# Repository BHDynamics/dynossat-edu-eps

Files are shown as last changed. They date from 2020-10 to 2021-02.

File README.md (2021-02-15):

# DynOSSAT-EDU-EPS (Electric Power System)
DynOSSAT-EDU is the first open source PocketQube educational kit compatible with CircuitPython and Arduino.

This plaform is equipped with all the necessary modules for the operation of a nanosatellite (PocketQube)
in Low Earth Orbit (LEO) that would serve as a device for teaching, training, and driving curiosity about the philosophy and technology related to NewSpace.

This repository contains the hardware files for the EPS (Electric Power System), the module responsible for battery management and power distribution subsystems,
including charging through solar panels using flight-proven MPPT electronics.

Hardware in this repository is licenced under **CERN OHL v1.2**.

## Technical details

- Well-known 48 MHz Cortex-M0 ATSAMD21E18 MCU with 256 KB flash + 32 KB RAM
- 32 Mbit SPI flash for storing CircuitPython code and libraries
- Flight-proven SPV1040 Maximum Power Point Tracking (MPPT) IC for solar cells power management
- Ultra low input voltage L6924D Lithium battery charger management IC optimized for pairing with the SPV1040
- Separate 5V and 3.3V power rails generated through high-performance DC/DC converters
- Battery Current/Voltage/Power measurement through the flight-proven INA226 digital meter
- Back-powering protection and load switching through the TPS22918, member of a flight-proven family of switches
- User-controllable WS2812B addressable RGB LED
- Female USB-C 2.0 connector for power and data logging
- Standard Molex Picoblade 1.5 mm connectors for battery and solar cells
- Connected to the OBC through SPI/I2C/UART for data communication and/or redundancy

## Documentation

Available in this repo's [Wiki](https://github.com/BHDynamics/dynossat-edu-eps/wiki).

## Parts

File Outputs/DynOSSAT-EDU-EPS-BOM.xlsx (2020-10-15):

Item | Qty | Reference(s) | Value | Part Number | Comments
1 | 2 | C1, C2 | 22pF |  | 0402 NP0 22pF
2 | 2 | C3, C17 | 1nF |  | 0402 NP0 1nF
3 | 10 | C4, C5, C6, C7, C8, C9, C14, C19, C23, C29 | 100nF |  | 0402 X7R/X5R 100nF
4 | 3 | C10, C12, C26 | 10nF |  | 0402 X7r/X5R 100nF
5 | 4 | C11, C18, C25, C27 | 1uF |  | 0402 1uF 10V or greater X5R or better
6 | 2 | C13, C30 | 10uF |  | 0603 10uF 10V or greater X5R or better
7 | 5 | C15, C16, C20, C22, C24 | 22uF |  | 0603 22uF 10V or greater X5R or better
8 | 1 | C21 | 4.7uF |  | 0603 4.7uF 10V or greater X5R or better
9 | 1 | C28 | 1uF |  | 0603 1uF 10V or greater X5R or better
10 | 2 | C31, C32 | 220uF | GRM31CR60J227ME11L | 1206 6.3V 220 uF
11 | 1 | D1 | WS2812B-MINI | WS2812B-MINI | RGB LED
12 | 2 | D2, D3 | LED_Small |  | 0603 LED. D2 Red, D3 Green
13 | 1 | D4 | LED_Small | SD05-01FTG | 5V TVS Diode SOD-323
14 | 5 | D5, D7, D8, D9, D10 | D_Schottky_Small | CUS10S30,H3F | Diode_SMD:D_SOD-323
15 | 1 | D6 | D_Schottky_Small | 1N5819HWQ-7-F | Diode_SMD:D_SOD-123
16 | 1 | F1 | Fuse_3A | T0603FF3000TM | Fuse:Fuse_0603_1608Metric
17 | 1 | J1 | Conn_01x05_Female | - | Connector_PinHeader_1.27mm:PinHeader_1x05_P1.27mm_Vertical
18 | 1 | J2 | USB_C_Receptacle_USB2.0 | U262-161N-4BVC11 | DynOSSAT:U262-161N-4BVC11
19 | 1 | J4 | PV Panel 1 | 53048-0210 | Connector_Molex:Molex_PicoBlade_53048-0210_1x02_P1.25mm_Horizontal
20 | 1 | J5 | PV Panel 2 | 53048-0210 | Connector_Molex:Molex_PicoBlade_53048-0210_1x02_P1.25mm_Horizontal
21 | 1 | J6 | Battery | 53048-0210 | Connector_Molex:Molex_PicoBlade_53048-0210_1x02_P1.25mm_Horizontal
22 | 1 | J7 | Main Bus PQBH40 | We don't have part numbers. Use generic brand | Pin header male 1.27mm pitch 2x20 vertical SMD
23 | 1 | J8 | Main Bus PQBH40 | We don't have part numbers. Use generic brand | Pin socket female 1.27mm pitch 2x20 vertical SMD
24 | 1 | JP1 | Jumper | We don't have part numbers. Use generic brand | Pin header male 1.27mm pitch 1x02 Vertical Through-Hole
25 | 1 | JP2 | Jumper | - | Solder jumper
26 | 1 | L1 | 22uH | SMNR4030-220MT | Inductor_SMD:L_Bourns-SRN4018
27 | 1 | L2 | 2.2uH | LQH32PN2R2NN0L | 1210 2.2uH Power Inductor
28 | 1 | L3 | 3.3uH | LQH32PN3R3NN0L | 1210 3.3uH Power Inductor
29 | 1 | Q1 | SQ3989EV | SQ3989EV-T1_GE3 | Dual P-Channel Mosfet
30 | 1 | Q2 | DMG2305 | DMG2305UX-7 | P-Channel Power Mosfet
31 | 7 | R1, R2, R3, R11, R18, R27, R32 | 100k |  | 0402 100k 1%
32 | 1 | R4 | 510R |  | 0402 510R 1%
33 | 2 | R5, R6 | 10k |  | 0402 10k 1%
34 | 1 | R7 | 0.002R | LVT06R0020HER | 0603 0.002R Current Shunt
35 | 2 | R10, R25 | 1M |  | 0402 1M
36 | 2 | R12, R13 | 330R |  | 0402 330R
37 | 3 | R14, R15, R16 | 1k |  | 0402 1k
38 | 1 | R17 | 0.033R | WSL0603R0330FEA | 0603 0.033R Current Shunt
39 | 1 | R19 | 22k2 |  | 0402 22.2k
40 | 1 | R20 | 2.2M |  | 0402 2.2M
41 | 1 | R21 | 820k |  | 0402 820k
42 | 2 | R22, R23 | 5.1k |  | 0402 5.1k
43 | 1 | R24 | 10M |  | 0402 10M
44 | 1 | R26 | 1.5M |  | 0402 1.5M
45 | 4 | R8, R9, R29, R33 | 47k |  | 0402 47k
46 | 1 | R30 | 88k |  | 0402 88k
47 | 2 | R31, R35 | 12k |  | 0402 12k
48 | 1 | R36 | 3k3 |  | 0402 3k3
49 | 1 | SW1 | SW_Push | 1TS002G-1800-3500-CT | Push Button side mount
50 | 1 | SW2 | SW_SPDT | OS102011MA1QN1 | SPDT switch
51 | 1 | U1 | ATSAMD21G18A | ATSAMD21G18A-MUT | MCU
52 | 1 | U2 | GD25Q32 | GD25Q32CNIGR | 32 Mbit flash memory SPI
53 | 1 | U3 | INA226 | INA226AIDGSR | Current/Voltage monitoring IC
54 | 1 | U4 | FP6291 | FP6291LR-G1 | Step-Up 2A DC-DC Boost Converter
55 | 4 | U5, U9, U10, U11 | TPS22918 | TPS22918DBVR | Load Switch
56 | 1 | U6 | SPV1040 | SPV1040T | Solar Power Harvester
57 | 1 | U7 | SY8089 | SY8089AAC | Step-Down 2A DC-DC Buck Converter
58 | 1 | U8 | L6924D | L6924D | Low Vin Battery Charger IC
59 | 1 | Y1 | 32.768 kHz - 12.5pF | X201232768KGD2SI | 2012 32768 kHz Crystal 12.5pF
For passives (resistors, capacitors, etc) you may use any quality brand while meeting requirements

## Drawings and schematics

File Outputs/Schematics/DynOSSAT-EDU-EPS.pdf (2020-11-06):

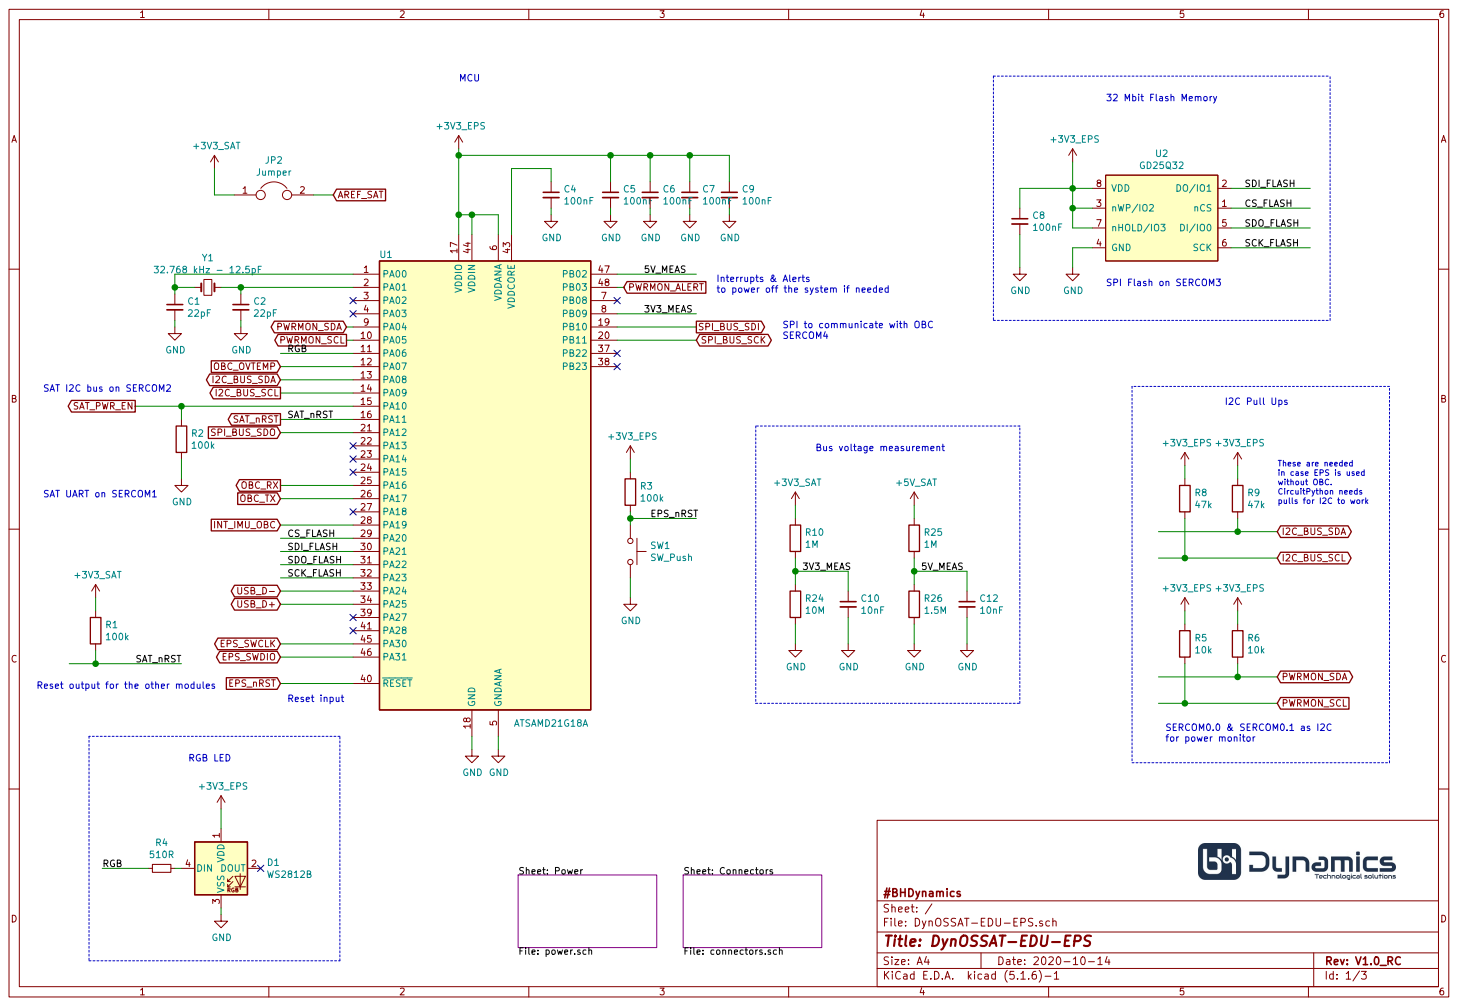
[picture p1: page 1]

in case EPS is used without OBC. CircuitPython needs pulls for I2C to work MCU

32 Mbit Flash Memory RGB LED

Interrupts & Alerts
to power off the system if needed

Id: 1/3 Title: DynOSSAT-EDU-EPS

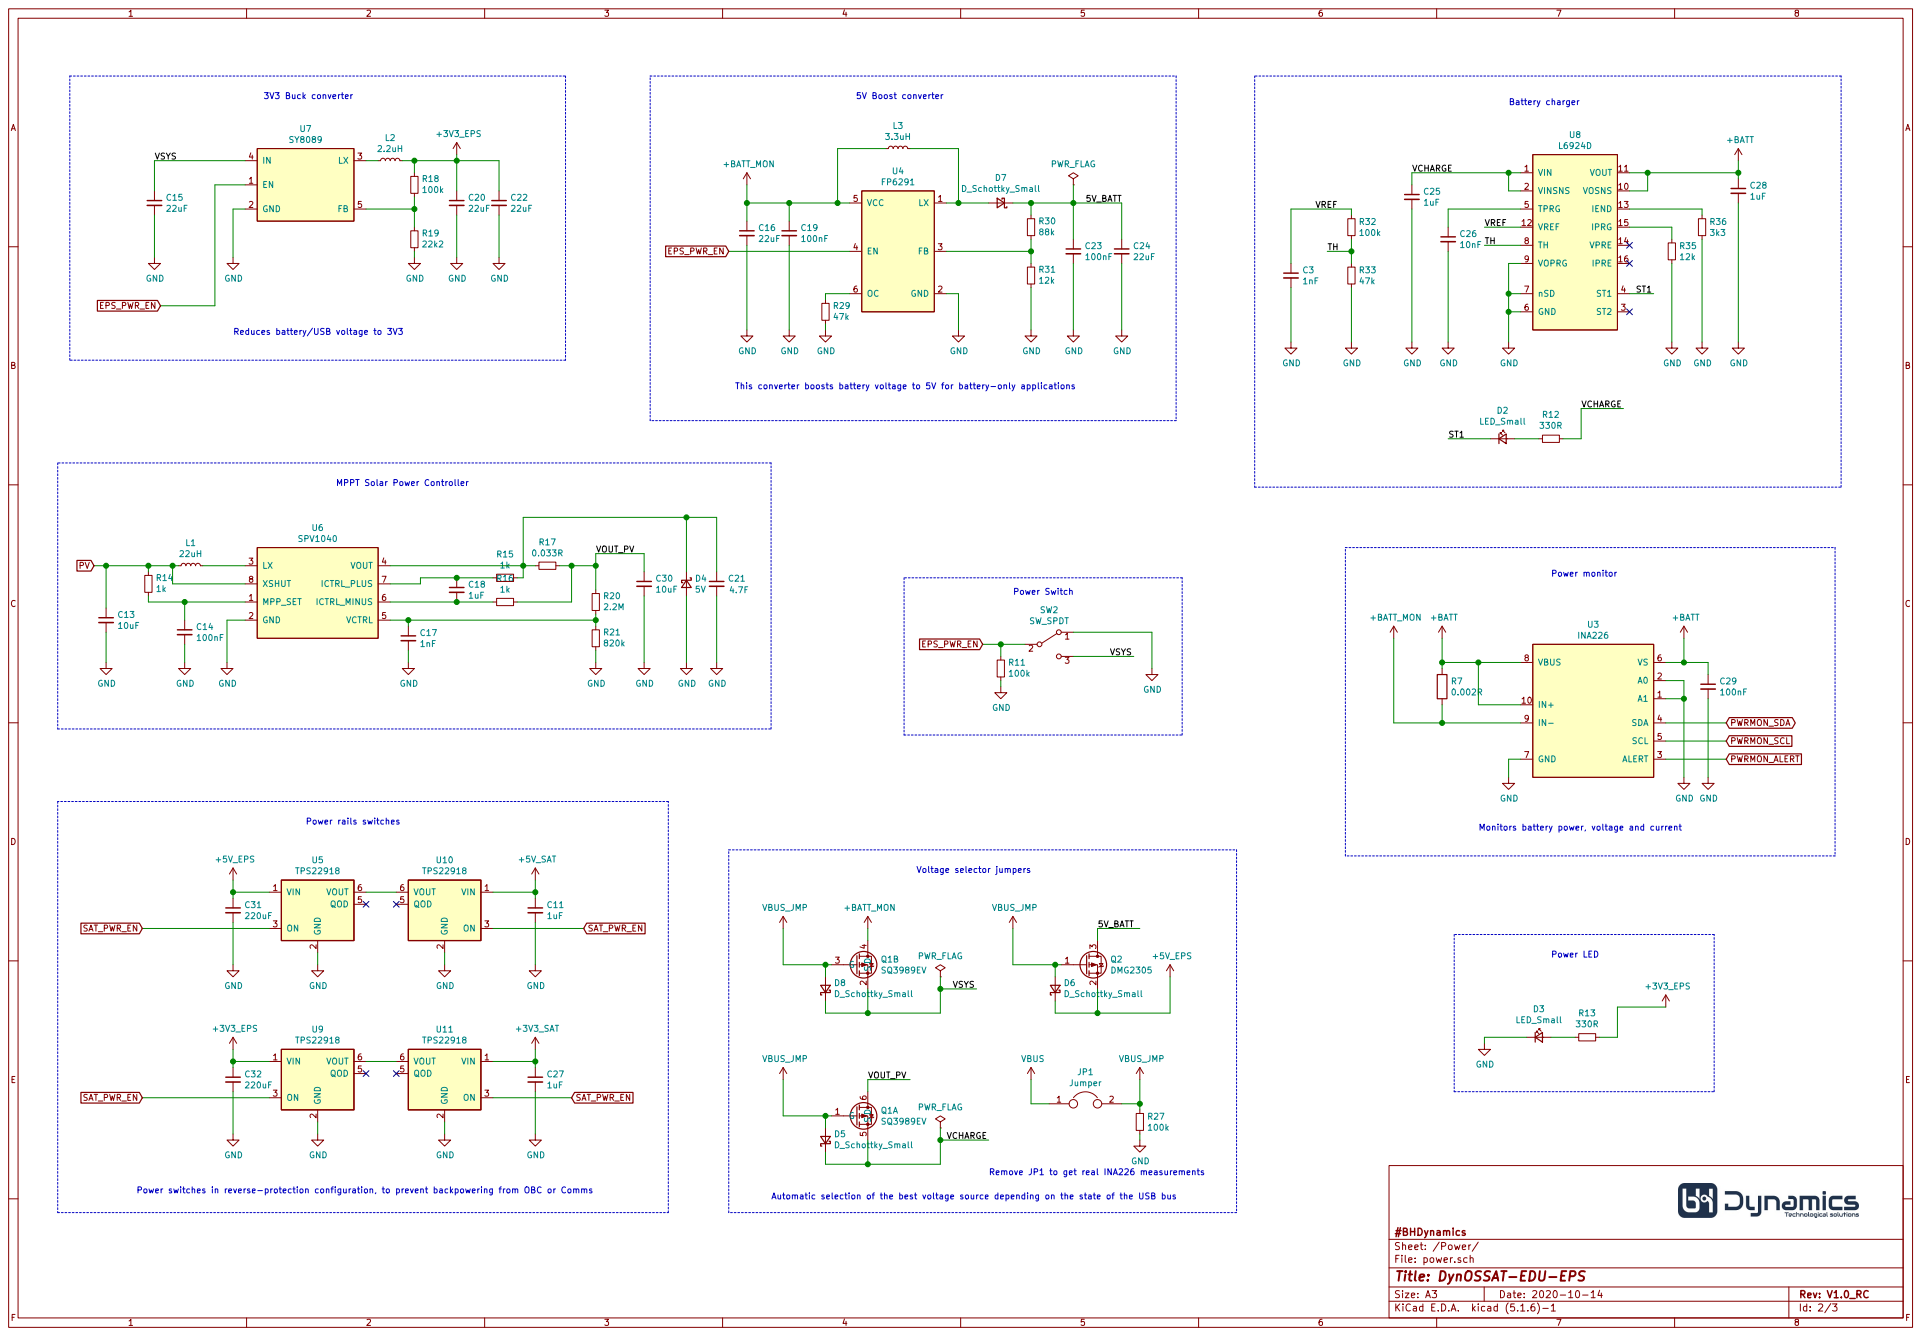
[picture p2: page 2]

2 ON 3 QOD 5 VOUT 6 U5 TPS22918 VIN 1 GND

2 ON 3 QOD 5 VOUT 6 U10 TPS22918 GND

2 ON 3 QOD 5 VOUT 6 U11 TPS22918 GND

Remove JP1 to get real INA226 measurements

Power switches in reverse-protection configuration, to prevent backpowering from OBC or Comms

File: power.sch Sheet: /Power/ #BHDynamics

Id: 2/3 Title: DynOSSAT-EDU-EPS

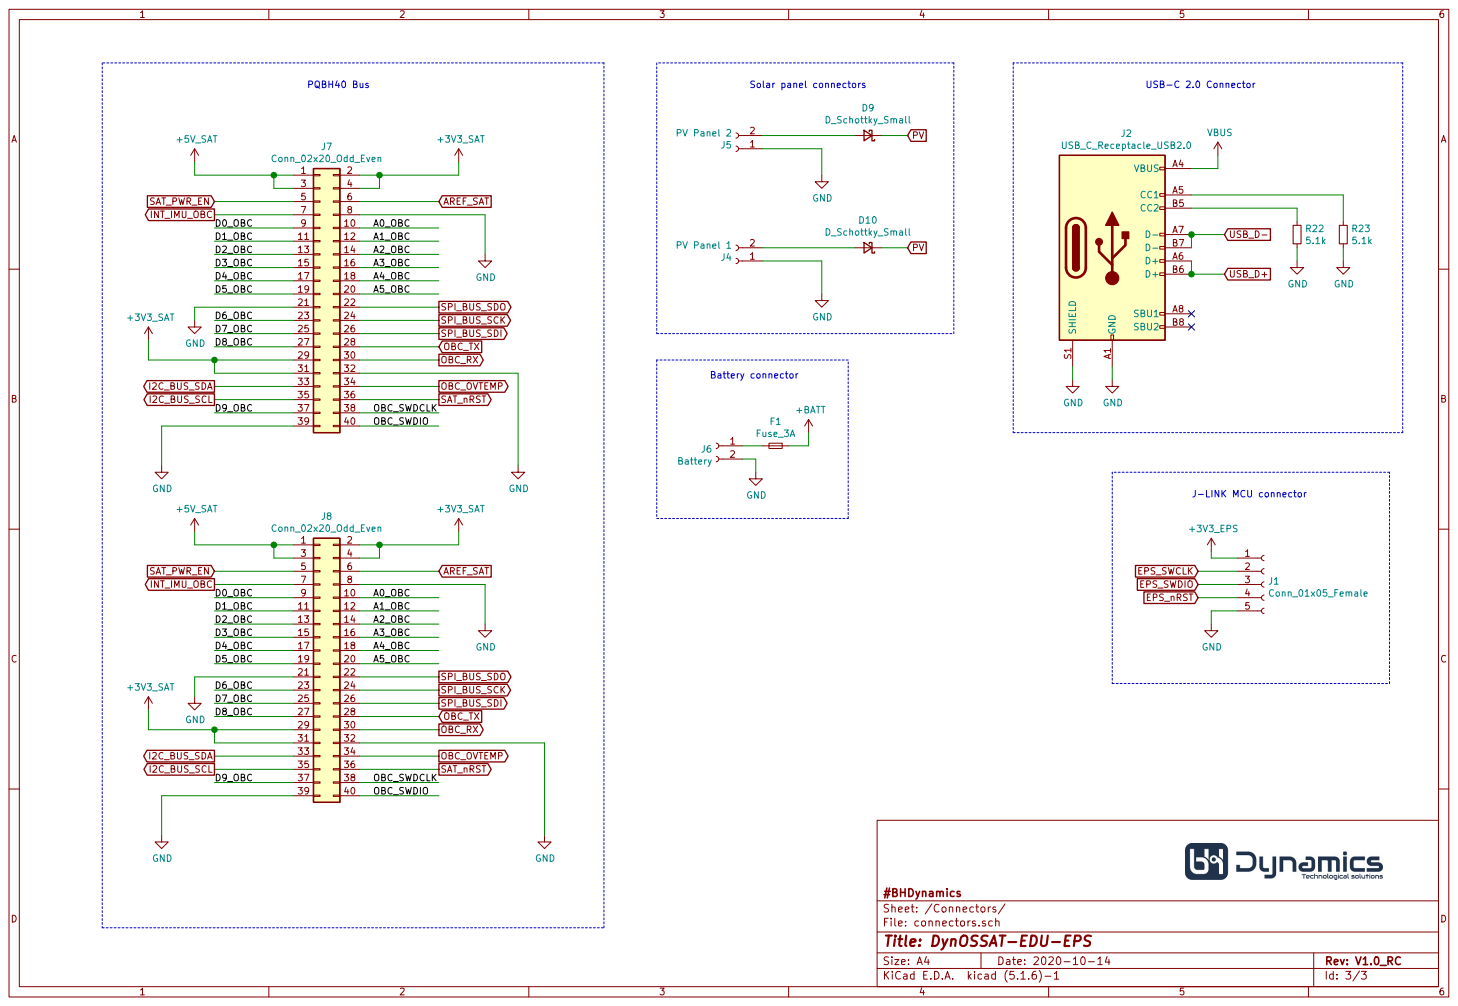
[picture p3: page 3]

File: connectors.sch Sheet: /Connectors/ #BHDynamics

Id: 3/3 Title: DynOSSAT-EDU-EPS

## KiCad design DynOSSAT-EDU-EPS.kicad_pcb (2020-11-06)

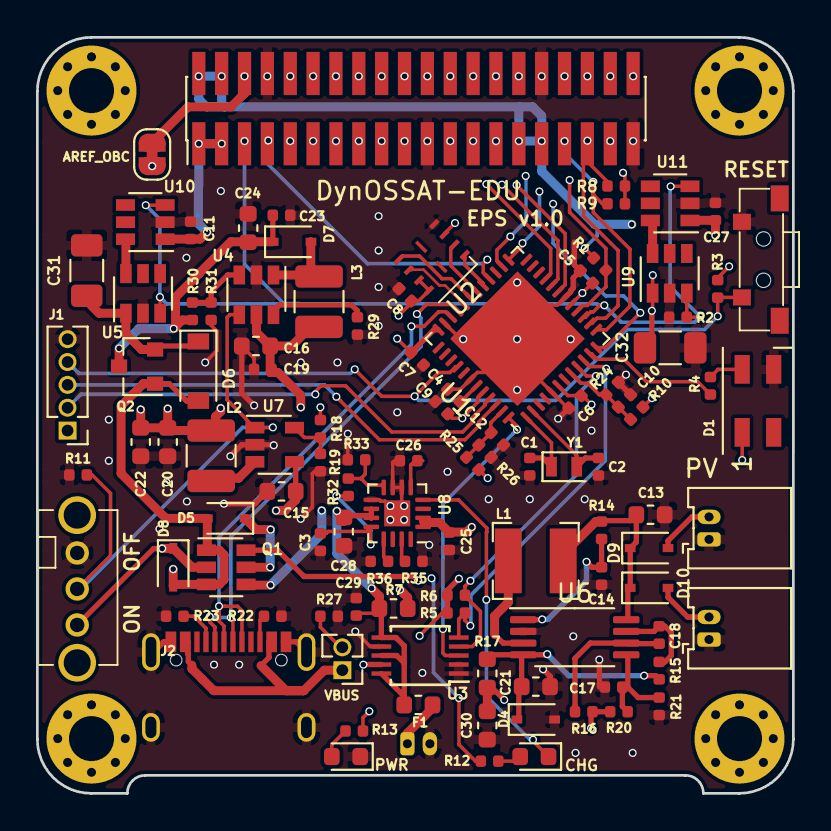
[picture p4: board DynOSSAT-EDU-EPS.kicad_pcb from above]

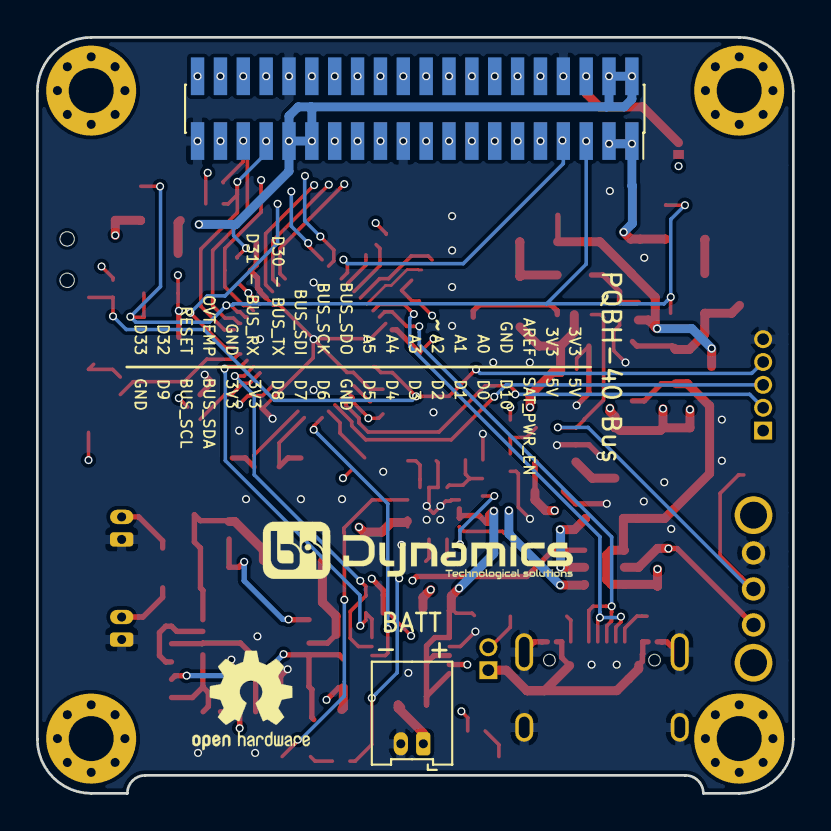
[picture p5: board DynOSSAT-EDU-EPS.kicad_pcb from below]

Board: 4 copper layers, 42.0 x 42.0 mm, 105 parts (2 on the bottom side), 90 nets.

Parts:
C1, C2: 22pF; C_0402_1005Metric
C3, C17: 1nF; C_0402_1005Metric
C4, C5, C6, C7, C8, C9, C14, C19, C23, C29: 100nF; C_0402_1005Metric
C10, C12, C26: 10nF; C_0402_1005Metric
C11, C18, C25, C27: 1uF; C_0402_1005Metric
C13, C30: 10uF; C_0603_1608Metric
C15, C16, C20, C22, C24: 22uF; C_0603_1608Metric
C21: 4.7F; C_0603_1608Metric
C28: 1uF; C_0603_1608Metric
C31, C32: 220uF; C_1206_3216Metric
D1: WS2812B; LED_SK6812MINI_PLCC4_3.5x3.5mm_P1.75mm
D2, D3: LED_Small; LED_0603_1608Metric
D4: 5V; D_SOD-323
D5, D7, D8, D9, D10: D_Schottky_Small; D_SOD-323
D6: D_Schottky_Small; D_SOD-123
F1: Fuse_3A; Fuse_0603_1608Metric
J1: Conn_01x05_Female; PinHeader_1x05_P1.27mm_Vertical
J2: USB_C_Receptacle_USB2.0; U262-161N-4BVC11
J4: PV Panel 1; Molex_PicoBlade_53048-0210_1x02_P1.25mm_Horizontal
J5: PV Panel 2; Molex_PicoBlade_53048-0210_1x02_P1.25mm_Horizontal
J6: Battery; Molex_PicoBlade_53048-0210_1x02_P1.25mm_Horizontal
J7: Conn_02x20_Odd_Even; PinHeader_2x20_P1.27mm_Vertical_SMD
J8: Conn_02x20_Odd_Even; PinSocket_2x20_P1.27mm_Vertical_SMD
JP1: Jumper; PinHeader_1x02_P1.27mm_Vertical
JP2: Jumper; SolderJumper-2_P1.3mm_Bridged_RoundedPad1.0x1.5mm
L1: 22uH; L_Bourns-SRN4018
L2: 2.2uH; L_1210_3225Metric
L3: 3.3uH; L_1210_3225Metric
Q1: SQ3989EV; SOT-23-6
Q2: DMG2305; SOT-23
R1, R2, R3, R11, R18, R27, R32: 100k; R_0402_1005Metric
R4: 510R; R_0402_1005Metric
R5, R6: 10k; R_0402_1005Metric
R7: 0.002R; R_0603_1608Metric
R8, R9, R29, R33: 47k; R_0402_1005Metric
R10, R25: 1M; R_0402_1005Metric
R12, R13: 330R; R_0402_1005Metric
R14, R15, R16: 1k; R_0402_1005Metric
R17: 0.033R; R_0603_1608Metric
R19: 22k2; R_0402_1005Metric
R20: 2.2M; R_0402_1005Metric
R21: 820k; R_0402_1005Metric
R22, R23: 5.1k; R_0402_1005Metric
R24: 10M; R_0402_1005Metric
R26: 1.5M; R_0402_1005Metric
R30: 88k; R_0402_1005Metric
R31, R35: 12k; R_0402_1005Metric
R36: 3k3; R_0402_1005Metric
SW1: SW_Push; 1TS002G-1800-3500-CT
SW2: SW_SPDT; OS102011MA1QN1
U1: ATSAMD21G18A; QFN-48-1EP_7x7mm_P0.5mm_EP5.3x5.3mm
U2: GD25Q32; WSON-8-1EP_3x4mm_P0.8mm
U3: INA226; TSSOP-10_3x3mm_P0.5mm
U4: FP6291; SOT-23-6
U5, U9, U10, U11: TPS22918; SOT-23-6
U6: SPV1040; TSSOP-8_4.4x3mm_P0.65mm
U7: SY8089; SOT-23-5
U8: L6924D; VQFN-16-1EP_3x3mm_P0.5mm_EP1.45x1.45mm
Y1: 32.768 kHz - 12.5pF; Crystal_SMD_2012-2Pin_2.0x1.2mm

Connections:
+3V3_EPS: C5.1, C6.1, C7.1, C8.1, C9.1, C20.1, C22.1, C32.1, D1.1, J1.1, L2.2, R3.1, R5.1, R6.1, R8.1, R9.1, R13.2, R18.2, U1.6, U1.17, U1.36, U1.44, U2.3, U2.7, U2.8, U9.1
+3V3_SAT: C27.1, J7.2, J7.4, J7.29, J7.31, J8.2, J8.4, J8.29, J8.31, JP2.1, R1.1, R10.1, U11.1
+5V_EPS: C31.1, D6.1, Q2.2, U5.1
+5V_SAT: C11.1, J7.1, J7.3, J8.1, J8.3, R25.1, U10.1
+BATT: C28.1, C29.1, F1.2, R7.1, U3.6, U3.8, U3.10, U8.10, U8.11
+BATT_MON: C16.1, C19.1, L3.1, Q1.4, R7.2, U3.9, U4.5
/3V3_MEAS: C10.1, R10.2, R24.1, U1.8
/5V_MEAS: C12.1, R25.2, R26.1, U1.47
/CS_FLASH: U1.29, U2.1
/Connectors/A0_OBC: J7.10, J8.10
/Connectors/A1_OBC: J7.12, J8.12
/Connectors/A2_OBC: J7.14, J8.14
/Connectors/A3_OBC: J7.16, J8.16
/Connectors/A4_OBC: J7.18, J8.18
/Connectors/A5_OBC: J7.20, J8.20
/Connectors/D0_OBC: J7.9, J8.9
/Connectors/D1_OBC: J7.11, J8.11
/Connectors/D2_OBC: J7.13, J8.13
/Connectors/D3_OBC: J7.15, J8.15
/Connectors/D4_OBC: J7.17, J8.17
/Connectors/D5_OBC: J7.19, J8.19
/Connectors/D6_OBC: J7.23, J8.23
/Connectors/D7_OBC: J7.25, J8.25
/Connectors/D8_OBC: J7.27, J8.27
/Connectors/D9_OBC: J7.37, J8.37
/Connectors/OBC_SWDCLK: J7.38, J8.38
/Connectors/OBC_SWDIO: J7.40, J8.40
/Power/5V_BATT: C23.1, C24.1, D7.1, Q2.3, R30.2
/Power/ST1: D2.1, U8.4
/Power/TH: R32.2, R33.1, U8.8
/Power/VCHARGE: C25.1, D5.1, Q1.5, R12.2, U8.1, U8.2
/Power/VOUT_PV: C30.1, Q1.6, R16.1, R17.1, R20.2
/Power/VREF: C3.1, R32.1, U8.12
/Power/VSYS: C15.1, D8.1, Q1.2, SW2.3, U7.4
/RGB: R4.2, U1.11
/SCK_FLASH: U1.32, U2.6
/SDI_FLASH: U1.30, U2.2
/SDO_FLASH: U1.31, U2.5
AREF_SAT: J7.6, J8.6, JP2.2
EPS_PWR_EN: R11.2, SW2.2, U4.4, U7.1
EPS_SWCLK: J1.2, U1.45
EPS_SWDIO: J1.3, U1.46
EPS_nRST: J1.4, R3.2, SW1.1, U1.40
GND: C1.2, C2.2, C3.2, C4.2, C5.2, C6.2, C7.2, C8.2, C9.2, C10.2, C11.2, C12.2, C13.2, C14.2, C15.2, C16.2, C17.2, C19.2, C20.2, C21.2, C22.2, C23.2, C24.2, C25.2, C26.2, C27.2, C28.2, C29.2, C30.2, C31.2, C32.2, D1.3, D3.1, D4.2, J1.5, J2.A1, J2.A12, J2.B1, J2.B12, J2.S1, J4.1, J5.1, J6.2, J7.8, J7.21, J7.32, J7.39, J8.8, J8.21, J8.32, J8.39, R2.2, R11.1, R19.1, R21.1, R22.2, R23.2, R24.2, R26.2, R27.2, R29.1, R31.1, R33.2, R35.2, R36.2, SW1.2, SW2.1, U1.5, U1.18, U1.35, U1.42, U1.49, U2.4, U3.1, U3.2, U3.7, U4.2, U5.2, U6.2, U7.2, U8.6, U8.7, U8.9, U8.17, U9.2, U10.2, U11.2
I2C_BUS_SCL: J7.35, J8.35, R8.2, U1.14
I2C_BUS_SDA: J7.33, J8.33, R9.2, U1.13
INT_IMU_OBC: J7.7, J8.7, U1.28
unnamed: C1.1, U1.1, Y1.1
unnamed: C2.1, U1.2, Y1.2
unnamed: C4.1, U1.43
unnamed: C14.1, R14.1, U6.1
unnamed: C17.1, R20.1, R21.2, U6.5
unnamed: C18.1, R15.2, U6.7
unnamed: C18.2, R16.2, U6.6
unnamed: C21.1, D4.1, R15.1, R17.2, U6.4
unnamed: C26.1, U8.5
unnamed: D1.4, R4.1
unnamed: D2.2, R12.1
unnamed: D3.2, R13.1
unnamed: D7.2, L3.2, U4.1
unnamed: D9.2, J5.2
unnamed: D10.2, J4.2
unnamed: F1.1, J6.1
unnamed: J2.A5, R23.1
unnamed: J2.B5, R22.1
unnamed: L1.2, U6.3
unnamed: L2.1, U7.3
unnamed: R18.1, R19.2, U7.5
unnamed: R29.2, U4.6
unnamed: R30.1, R31.2, U4.3
unnamed: R35.1, U8.15
unnamed: R36.1, U8.13
unnamed: U5.6, U10.6
unnamed: U9.6, U11.6
OBC_OVTEMP: J7.34, J8.34, U1.12
OBC_RX: J7.30, J8.30, U1.25
OBC_TX: J7.28, J8.28, U1.26
PV: C13.1, D9.1, D10.1, L1.1, R14.2, U6.8
PWRMON_ALERT: U1.48, U3.3
PWRMON_SCL: R5.2, U1.10, U3.5
PWRMON_SDA: R6.2, U1.9, U3.4
SAT_PWR_EN: J7.5, J8.5, R2.1, U1.15, U5.3, U9.3, U10.3, U11.3
SAT_nRST: J7.36, J8.36, R1.2, U1.16
SPI_BUS_SCK: J7.24, J8.24, U1.20
SPI_BUS_SDI: J7.26, J8.26, U1.19
SPI_BUS_SDO: J7.22, J8.22, U1.21
USB_D+: J2.A6, J2.B6, U1.34
USB_D-: J2.A7, J2.B7, U1.33
VBUS: J2.A4, J2.A9, J2.B4, J2.B9, JP1.1
VBUS_JMP: D5.2, D6.2, D8.2, JP1.2, Q1.1, Q1.3, Q2.1, R27.1

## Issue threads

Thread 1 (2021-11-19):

L6924D Maximum charging time

AlbertoZandara, 2021-11-19:
Reading your schematic, I noticed you selected a Ctprg = 10nF. It means the maximum charging time of the L6924D is set to around 90 minutes. Isn't it a problem?
Assuming to have a low power production from the solar panels, after 90 minutes the battery will definitely be not completely charge. Consequently, according to the L6924D datasheet, the battery charger IC shoud start a FAULT chart remaining in some sort of an infinite loop. How did you avoid this behaviour?
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

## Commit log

2020-10-15 First commit RC 1.0
    [DynOSSAT-EDU-EPS-BOM.xlsx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]
2020-11-06 Change MISO/MOSI for SDI/SDO
    Update library to latest version
    [DynOSSAT-EDU-EPS-B_Cu.gbr, DynOSSAT-EDU-EPS-B_Fab.gbr, DynOSSAT-EDU-EPS-B_Mask.gbr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]
